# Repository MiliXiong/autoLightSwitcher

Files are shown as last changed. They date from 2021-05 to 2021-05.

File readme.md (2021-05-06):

# 灯控开关：人体感应灯控

可以直接套在标准的灯开关上，通过单片机控制原有开关的通断。

实例是用于卫生间的人体红外感应灯控。

此项目包含了3D模型、电路图和代码。

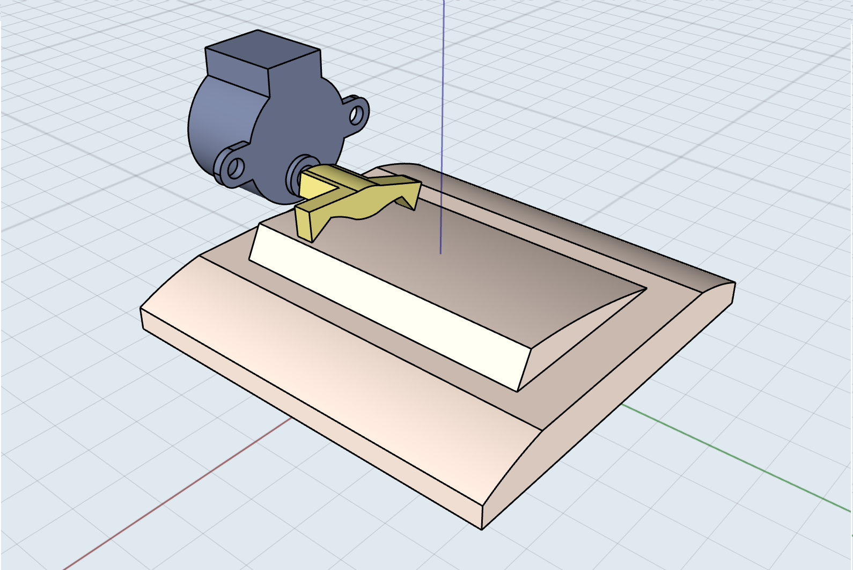
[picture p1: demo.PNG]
demo


3D模型：

1. [灯开关控制盒-压杆](https://github.com/MiliXiong/autoLightSwitcher/blob/master/3D%20%E6%A8%A1%E5%9E%8B/STL%20%E5%8F%AF%E7%9B%B4%E6%8E%A5%E6%89%93%E5%8D%B0%E6%96%87%E4%BB%B6/%E7%81%AF%E5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) 
1. [灯开关控制盒-外罩](https://github.com/MiliXiong/autoLightSwitcher/blob/master/3D%20%E6%A8%A1%E5%9E%8B/STL%20%E5%8F%AF%E7%9B%B4%E6%8E%A5%E6%89%93%E5%8D%B0%E6%96%87%E4%BB%B6/%E7%81%AF%E5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)
1. [红外传感器盒-外壳](https://github.com/MiliXiong/autoLightSwitcher/blob/master/3D%20%E6%A8%A1%E5%9E%8B/STL%20%E5%8F%AF%E7%9B%B4%E6%8E%A5%E6%89%93%E5%8D%B0%E6%96%87%E4%BB%B6/%E7%BA%A2%E5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)
1. [红外传感器盒-底板](https://github.com/MiliXiong/autoLightSwitcher/blob/master/3D%20%E6%A8%A1%E5%9E%8B/STL%20%E5%8F%AF%E7%9B%B4%E6%8E%A5%E6%89%93%E5%8D%B0%E6%96%87%E4%BB%B6/%E7%BA%A2%E5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)

核心元件：

1. 单片机：stc8h1h28
1. 步进电机：28byj48
1. 电机驱动：ULN2003
1. 人体热释红外感应器：HC-SR501
1. 锂电池充电芯片：TP5400
1. 电池：18650

使用效果：https://www.bilibili.com/video/BV1vf4y1p7HE

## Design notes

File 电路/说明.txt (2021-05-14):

Altium Designer是立创EDA导出的，有限建议使用立创EDA。
电池满电压是4.2V，单个2000mAh锂电池充满电续航时间在15天以上。

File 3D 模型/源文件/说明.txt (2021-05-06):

灯开关控制盒是 iPad 上的shapr3D软件画的。
红外感应器盒子是solidworks画的

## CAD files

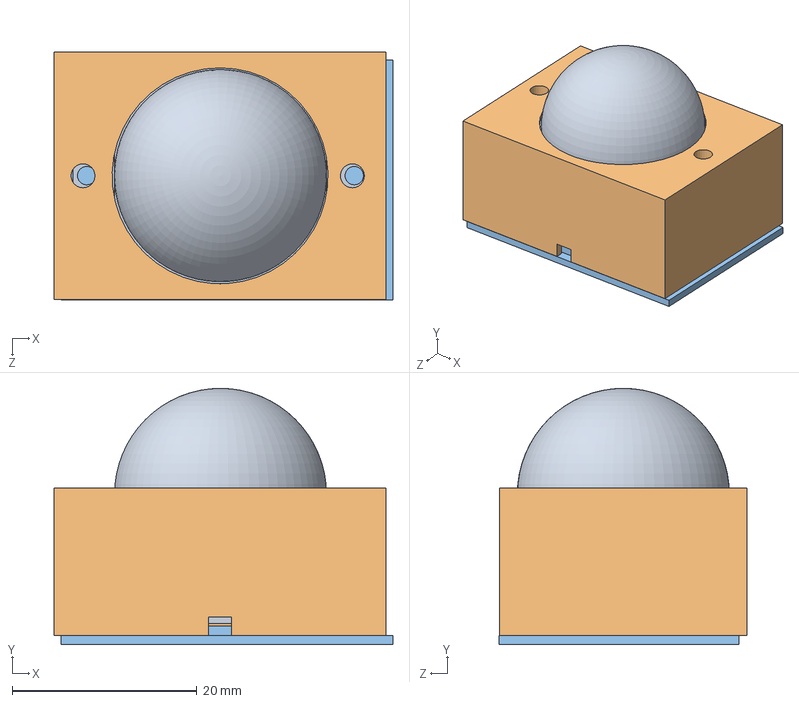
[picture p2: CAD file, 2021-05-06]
3D 模型/源文件/红外感应器盒子-solidworks/宿舍灯控.SLDASM
36.7 x 27.8 x 26.8 mm
红外人体感应模块
红外盒子
红外壳子底板

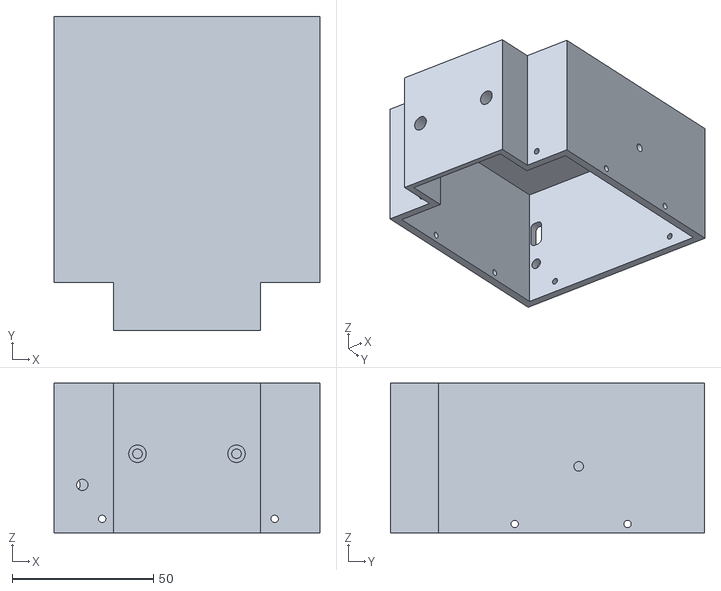
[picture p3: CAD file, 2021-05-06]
3D 模型/STL 可直接打印文件/灯开关控制盒-外罩.stl
94.0 x 111.0 x 53.0

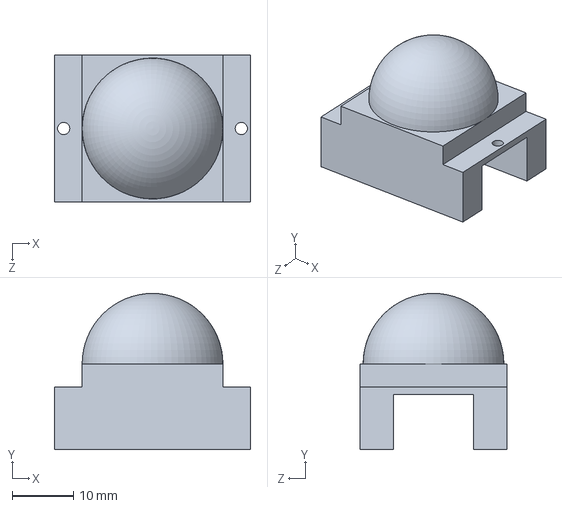
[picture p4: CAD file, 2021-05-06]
3D 模型/源文件/红外感应器盒子-solidworks/红外人体感应模块.SLDPRT
32.0 x 25.5 x 24.0 mm

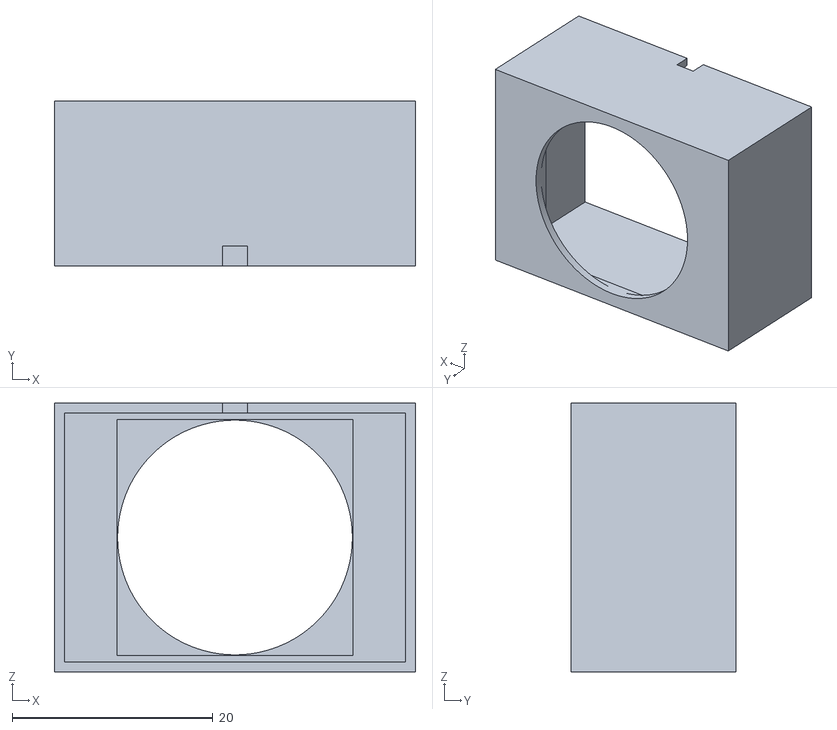
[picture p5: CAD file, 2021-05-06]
3D 模型/STL 可直接打印文件/红外传感器盒子-外壳.STL
36.0 x 16.5 x 26.8

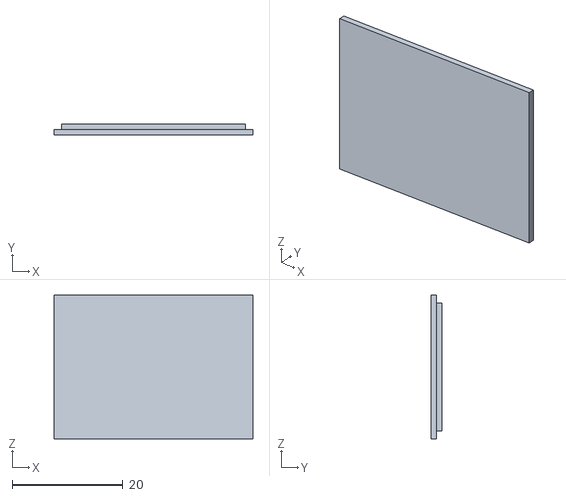
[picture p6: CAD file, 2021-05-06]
3D 模型/STL 可直接打印文件/红外传感器盒子-底板.STL
36.0 x 2.00 x 26.0

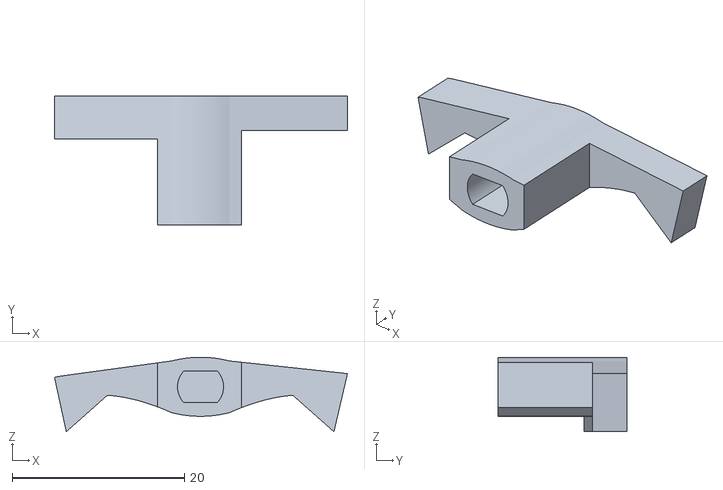
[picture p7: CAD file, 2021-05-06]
3D 模型/STL 可直接打印文件/灯开关控制盒-压杆.stl
34.0 x 15.0 x 8.64

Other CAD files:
代码/Objects/main.obj
3D 模型/源文件/红外感应器盒子-solidworks/红外盒子.SLDPRT
代码/Objects/STARTUP.obj
3D 模型/源文件/红外感应器盒子-solidworks/红外壳子底板.SLDPRT

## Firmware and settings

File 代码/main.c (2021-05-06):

#include "stc8h.h" //you can also put this head file under the folder: "C:\Program Files (x86)\keil5\C51\INC\STC\"
sbit Hsensor=P3^2;
sbit Touchout=P3^3;

#define Pmotor(x) (P1=P1&0xf0|x)
#define MOTOR_DELAY 30

#define CONTROL_AUTO 1
#define CONTROL_MANUAL 0

#define LIGHT_ON 1
#define LIGHT_OFF 0

#define TOUCH_SHORT 2
#define TOUCH_LONG 1
#define TOUCH_INACTIVE 0

#define SENSOR_ACTIVE 1
#define SENSOR_INACTIVE 0

#define WAIT_ON 1
#define WAIT_OFF 0

#define MOTOR_A 0x01
#define MOTOR_AB 0x03
#define MOTOR_B 0x02
#define MOTOR_BC 0x06
#define MOTOR_C 0x04
#define MOTOR_CD 0x0C
#define MOTOR_D 0x08
#define MOTOR_DA 0x09
#define MOTOR_DOWN 0x00

#define MOTOR_STEP_GO 25
#define MOTOR_STEP_BACK 45

unsigned char light_state=LIGHT_OFF;
unsigned char sensor_state=SENSOR_INACTIVE;
unsigned char touch_state=TOUCH_INACTIVE;
unsigned char control_mode=CONTROL_MANUAL;
unsigned char wait_state=WAIT_OFF;

void delay_ms(unsigned int interval)
{
	int i,j;
		for(i=interval;i>0;i--)
			for(j=0;j<400;j++);
}

void motor(int step)
{
	int ctn=0;
	P1M0|=0x0F;
	P1M1&=~0x0F;
	delay_ms(100); 
	if(step>0)
	{
		while(++ctn<=step){
			Pmotor(MOTOR_A);
			delay_ms(MOTOR_DELAY);
			Pmotor(MOTOR_AB);
			delay_ms(MOTOR_DELAY);
			Pmotor(MOTOR_B);
			delay_ms(MOTOR_DELAY);
			Pmotor(MOTOR_BC);
			delay_ms(MOTOR_DELAY);
			Pmotor(MOTOR_C);
			delay_ms(MOTOR_DELAY);
			Pmotor(MOTOR_CD);			
			delay_ms(MOTOR_DELAY);
			Pmotor(MOTOR_D);
			delay_ms(MOTOR_DELAY);
			Pmotor(MOTOR_DA);			
			delay_ms(MOTOR_DELAY);
		}
	}
	else{
		while(++ctn<=-step){
			Pmotor(MOTOR_D);
			delay_ms(MOTOR_DELAY);
			Pmotor(MOTOR_CD);			
			delay_ms(MOTOR_DELAY);
			Pmotor(MOTOR_C);
			delay_ms(MOTOR_DELAY);
			Pmotor(MOTOR_BC);
			delay_ms(MOTOR_DELAY);
			Pmotor(MOTOR_B);
			delay_ms(MOTOR_DELAY);
			Pmotor(MOTOR_AB);
			delay_ms(MOTOR_DELAY);
			Pmotor(MOTOR_A);
			delay_ms(MOTOR_DELAY);
			Pmotor(MOTOR_DA);
			delay_ms(MOTOR_DELAY);
		}
	}
	Pmotor(MOTOR_DOWN);
	P1M0&=~0x0F;
	P1M1|=0x0F;
}
	

void init_all()
{
	// P3.2 for sensor input. interrup.t (rising or fulling edge trigger)
	// high restance state by default
	IT0=0;
	EX0=1;
	
	// P3.3 for touch pad input. interrup.t (rising edge trigger)
	// high restance state by default
	IT1=0;
	EX1=1;
	// P1 port should be set as output state before being used, and after that P1 should be set as high resitance state.
	// P1 port is at high resitance state by default.

	// TIMER
	//TMOD=0x00;

	EA=1;
}

void timer_start()
{
	// lowpower timer,period: 2s
	WKTCL=0xff;
	WKTCH=0x0f;
	WKTCH|=0x80;
}

void timer_stop()
{
	WKTCH&=~0x80;
}

// sensor's interrup.t
void int0_int() interrupt 0
{
	EX0=0;
	//no operation, as the main program will judge the Hsensor pin
	EX0=1;
}

// touchpad's interrup.t
void int1_int() interrupt 2
{
	unsigned int ctn=0;
	EX1=0;
	delay_ms(30);
	if(Touchout==1){
		for(ctn=0;ctn<500;ctn++){
			delay_ms(30);
			if(Touchout==0){
				break;
			}
		}
		if(ctn<100){
			touch_state=TOUCH_SHORT;
		}
		else{
			touch_state=TOUCH_LONG;
		}
	}
	EX1=1;
}

void light_on()
{
	if(light_state==LIGHT_OFF){
		light_state=LIGHT_ON;
		motor(-MOTOR_STEP_GO);
		motor(MOTOR_STEP_BACK);
	}
}
void light_off()
{
	if(light_state==LIGHT_ON){
		light_state=LIGHT_OFF;
		motor(MOTOR_STEP_GO);
		motor(-MOTOR_STEP_BACK);
	}
}
void go_automode()
{
	control_mode=CONTROL_AUTO;
	if(Hsensor==1){
		light_state=LIGHT_OFF;
		light_on();
	}else{
		light_state=LIGHT_ON;
		light_off();
	}
}
void go_manualmode()
{
	timer_stop();
	wait_state=WAIT_OFF;
	control_mode=CONTROL_MANUAL;
	motor(-120);
}



void lowpower()
{
	PCON=0x02;  // turn to "power down" mode
}


void main()
{
	unsigned int sensor_inact_ctn=0;
//	P1M0|=0x0F;
//	P1M1&=~0x0F;
//	P1=0xFF;
//	while(1);
//	while(1){
	delay_ms(1000);
	init_all();
//	light_on();
//	}

	while(1){
		switch(touch_state)
		{
			case TOUCH_SHORT:
				touch_state=TOUCH_INACTIVE;
				if(control_mode==CONTROL_MANUAL)
				{
					switch(light_state)
					{
						case LIGHT_ON:
							light_off();
						break;
						case LIGHT_OFF:
							light_on();
						break;
					}
				}
			break;
			case TOUCH_LONG:
				touch_state=TOUCH_INACTIVE;
				switch(control_mode)
				{
					case CONTROL_AUTO:
						go_manualmode();
					break;
					case CONTROL_MANUAL:
						go_automode();
					break;
				}
			break;
		}
		
		if(control_mode==CONTROL_AUTO){
				if(Hsensor==1){
					if(wait_state==WAIT_ON){  
						timer_stop();
						wait_state=WAIT_OFF;
					}						
					light_on();	
				}
				else if(Hsensor==0){
					if(wait_state==WAIT_OFF){
						wait_state=WAIT_ON; // wait for several seconds or minutes to detecing the sensor state after the sensor sending the low-voltage signal
						sensor_inact_ctn=0;
						timer_start();
					}
					if (++sensor_inact_ctn>15){  // you can change 15 to set other waiting & detecing time.
						timer_stop();
						light_off();
					}
				}
		}
		lowpower();
		delay_ms(10); 
	}
	
}
